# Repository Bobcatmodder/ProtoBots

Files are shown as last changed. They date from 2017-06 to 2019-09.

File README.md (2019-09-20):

# The ProtoBot project

https://theprotobotproject.wordpress.com

https://www.instructables.com/id/How-to-Build-the-ProtoBot-a-100-Open-Source-Super-/

Welcome! The goal of this project to create a robot platform that's

Simple and easy to use

    With a total of 2 motors, and 4 sensors, the ProtoBot is a very simple robot.
    Don’t let it fool you, though! You can still do a lot with it, especially with programming. 
    It’s also very easy to build. In our experience, a middleschooler can build one in several
    hours, including soldering the board.

Low Cost and Accessible

    Using cheap, common components, the ProtoBot is easily sourced online. The plastic parts 
    can be printed on any 3D printer that has a  build volume over 10x10x5, or ordered from a
    3D printing service online. The PCB can be either hand etched, or obtained through a 
    PCB prototyping service.

100% Open Source

    Everything is open source, even the guides. That means anyone can:

      Download all design files, source code, and documentation free of charge
      Modify all or any part of the work
      Distribute the original, or modified versions of the work
      Sell copies of the original, or modified work

NOTE: Still a work in progress- If anything's missing, please contact me!

Liscense notes:
    All the hardware design files, and Arduino software/programs are under MIT liscenses. 
    All the Guides and instructions are under CC Attriution 4.0 liscenses. 

    To credit me on a website or document, simply link to my GitHub here. PCBs and STL files need not include any form of direct credit, assuming any modified versions you upload to the internet have a link to my GitHub, credited as the original project. Code can simply have a line at the top that says something like "Based off of original code by Jacob Field, the ProtoBotProject" and a the GitHub URL. Basically, make sure people are able to find the original project from your modification, if they wish.

If you have any questions about this or anythign else, feel free to contact me. There's a contact form on the website that goes directly to my personal email.

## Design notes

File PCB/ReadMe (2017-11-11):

Etchable and Gerber files for the circuit boards. 

I've used PCBWay to make the boards, and so far I've been quite happy with both quality and prices.

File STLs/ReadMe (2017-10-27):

STL files. 
These can be printed at 0.2 MM resolution, and require no rafts or supports.

Usually I print the base at 103% scale, and the antenna parts at 105%, to ensure everything fits. It depends on how precise your printer is. I also usually scale the PCB supports to be twice as tall, cause they're not really tall enough as is.

The "4Antenna" file is just 4 antenna pieces in one STL, so that you can fit more on a printbed.

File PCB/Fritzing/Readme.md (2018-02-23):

Here are the fritzing files for the PCB, in case anyone wants to modify it.

Ideally you should credit my original design somewhere on the board, linking to the GitHub, or at least including the keywords "ProtoBot", if you release your own version.
Linking to the github isn't nessesary if you link to my original project here on your project page.

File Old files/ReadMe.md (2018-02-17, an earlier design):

A place to keep all the old files and such, in case anyone needs them.

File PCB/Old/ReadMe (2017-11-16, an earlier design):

These are older board designs. I'm just keeping them around in case newer versions don't work.

Should be functionally the same, but missing the Open Source Hardware logo and website URL,
as well as a few minor resistor placement changes and silkscreen images.

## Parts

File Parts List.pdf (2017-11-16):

## ProtoBot parts list:

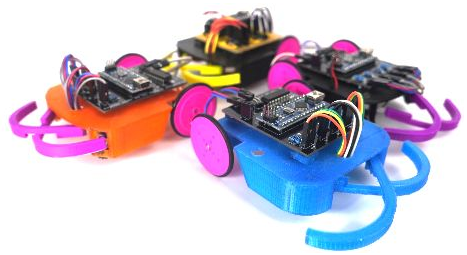
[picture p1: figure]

Quantities are enough for 1 complete robot

- 2 x N20 Gear motors (http://www.ebay.com/itm/6-12V-300-600-30RPM-Mini-DC-Metal-Gear-Motor-with-Gearwheel-Shaft-Diameter-N20-/172367169254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) (300RPM, 12V)
- 1 x Plastic Wheels (https://www.ebay.com/itm/10PCS-18-20-22-30-39mm-Synchronous-Belt-Triangle-Plastic-Pulley-Wheel-Toy-Parts/331665282711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) (39mm Yellow (3mm) - One lot is enough for 5 robots)
- 1 x Tactile Switches (http://www.ebay.com/itm/Pro-10PCS-Tact-Switch-KW11-3Z-5A-250V-Microswitch-3PIN-Buckle-Black-New-Arrivals-/391646361528) (Bump Sensors, One lot is enough for 5 robots)
- 1 x L293D Motor Driver IC (https://www.ebay.com/itm/2Pcs-L293D-L293-Push-Pull-Four-Channel-Motor-Driver-IC-NEW-C/141976513714) (One lot is enough for 2 robots)
- 1 x Wires (https://www.ebay.com/itm/40Pcs-1P-1P-2Pin-Header-2-54mm-Female-to-Female-Dupont-Line-Connector-Wire-Cable/282271776128) (Female to female jumper wires - One lot is enough for 4 robots)
- 1 x Headers (http://www.ebay.com/itm/5pcs-1-40-40Pin-2-54mm-20mm-Long-Header-Pin-Male-Breakable-Pin-Header-CA-/141976508934) (One lot is enough for 10 robots)
- 1 x 9V battery Clips (http://www.ebay.com/itm/10-pcs-9V-9-Volt-Battery-Clip-Connector-Soft-Shell-Black-w9-/172489325525) (One lot is enough for 10 robots)
- 1 x 10K resistors (http://www.ebay.com/itm/100pcs-1-4w-Watt-10K-ohm-10Kohm-Metal-Film-Resistor-0-25W-100000R-1-/141976458420) (One lot is enough for 25 robots)
- 1 x 220 Ohm resistors (https://www.ebay.com/itm/100-PCS-1-4W-0-25W-5-220-R-OHM-Carbon-Film-Resistor-1st-Class-Postage-UK-U5C7/332361071234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) (One lot is enough for 50 robots)
- 1 x Arduino Nano (https://www.ebay.com/itm/1-2-5-PCS-USB-Nano-V3-0-ATmega168-16M-5V-Mini-controller-CH340G-For-Arduino/253086177630) (ATEMGA328P module, not interface base module)
- 1 x Reflective IR optical sensor (http://www.ebay.com/itm/252618720538?_trksid=p2055119.m1438.l2649&ssPageName=STRK%3AMEBIDX%3AIT) (Enough for 5 robots, here’s (https://www.ebay.com/itm/100PCS-TCRT5000L-TCRT5000-Reflective-Optical-Sensor-Infrared-IR-Switch-infrared/253141705866) enough for 50)
- 1 x Female header pins (https://www.ebay.com/itm/10X-Single-Row-Straight-Female-Pin-Header-Connector-Strip-Arduino-2-54mm-CB/201874127141) (One lot is enough for a lot of robots)

Links updated 11/16/17

Copyright © 2017, Jacob Field. This work is licensed under a Creative Commons Attribution 4.0 International License. (http://creativecommons.org/licenses/by/4.0/)

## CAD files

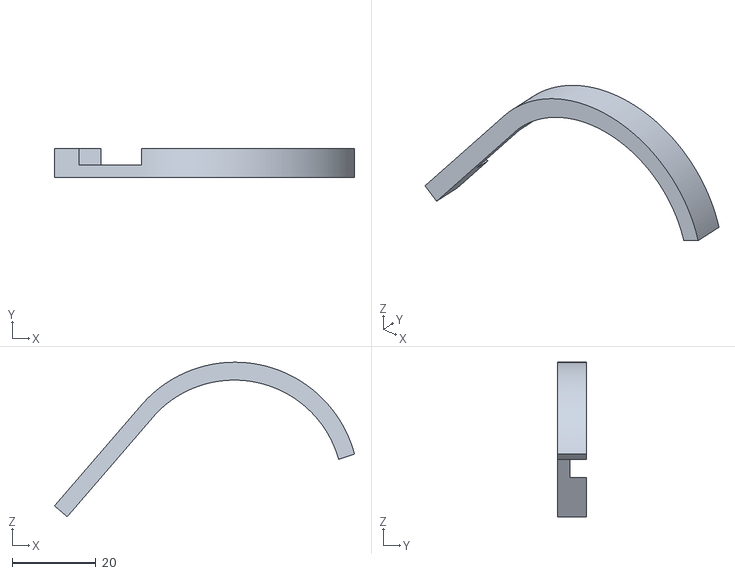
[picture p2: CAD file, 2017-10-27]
STLs/Antenna.stl
71.6 x 7.00 x 36.9

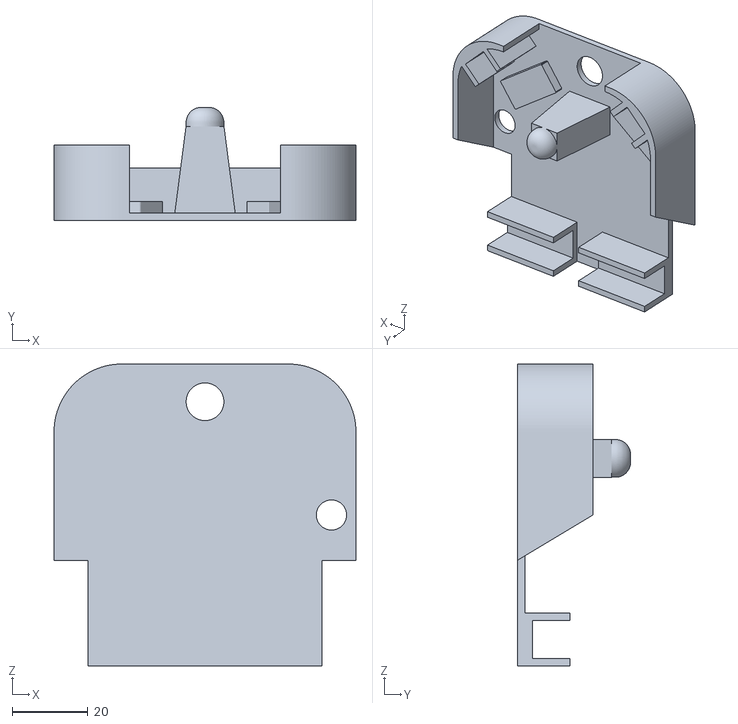
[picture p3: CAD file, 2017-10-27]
STLs/Base.stl
80.0 x 30.0 x 80.0

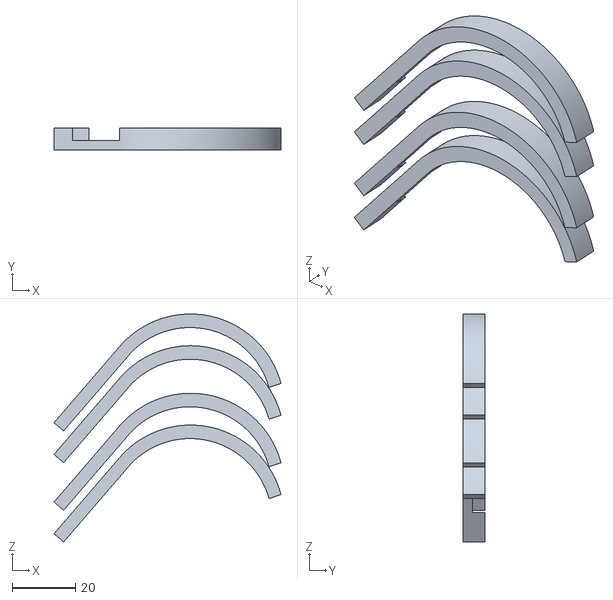
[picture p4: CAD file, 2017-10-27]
STLs/4Antenna.stl
71.6 x 7.00 x 71.9

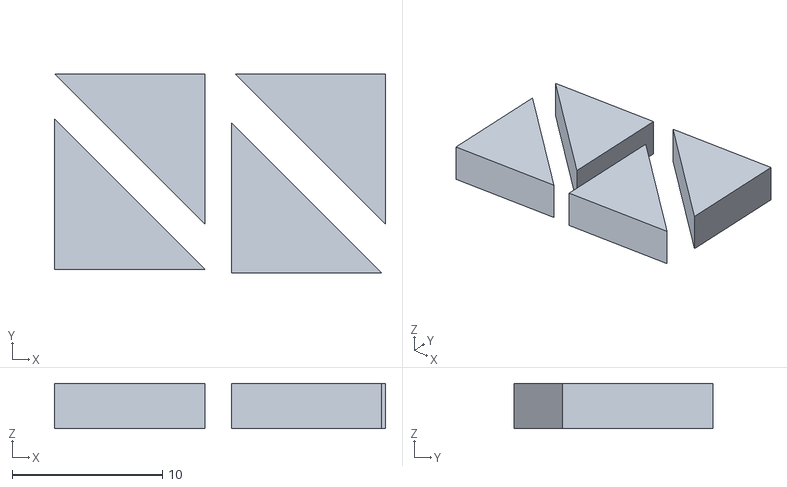
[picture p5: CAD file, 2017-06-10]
STLs/ProtoBotPCBSupport.stl
22.0 x 13.2 x 3.00

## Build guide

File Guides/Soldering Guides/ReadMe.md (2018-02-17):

These are guides for soldering the different major components in the ProtoBot.

For an online (Instructables) version, visit https://www.instructables.com/id/How-to-Build-the-ProtoBot-a-100-Open-Source-Super-/

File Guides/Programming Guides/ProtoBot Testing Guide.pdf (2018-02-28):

## Testing your Protobot

Now that your protobot is built, let’s test it to make sure everything works!

Plug the robot into your computer, using a USB cable.

On the desktop, look for the Arduino icon. If you can’t find it there, try searching for “Arduino” in the start menu.

Double click the icon to start the Arduino editor.

Once the Arduino IDE
is started, click on
“File”, then
“Examples”, and scroll
all the way down.

You should see
“ProtoBotV03”. Click
on that, and then
click on
“ProtoBotExplorer”.

This is the example
program we’ll use to
test your robot.

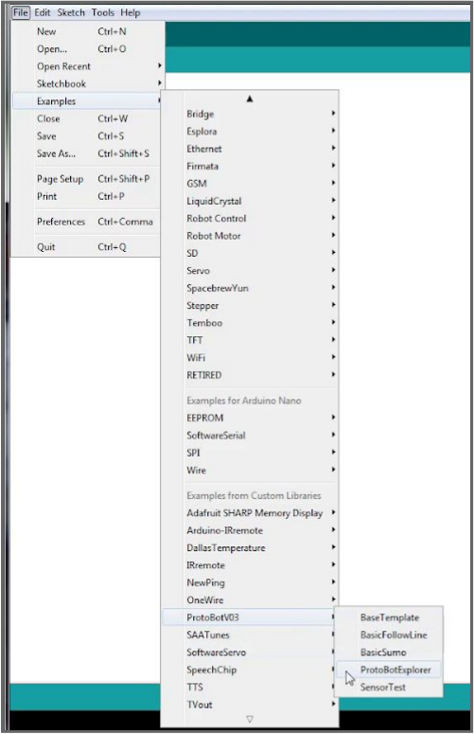
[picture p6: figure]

Copyright © 2017, Jacob Field. This work is licensed under a Creative Commons Attribution 4.0 International License. (http://creativecommons.org/licenses/by/4.0/)

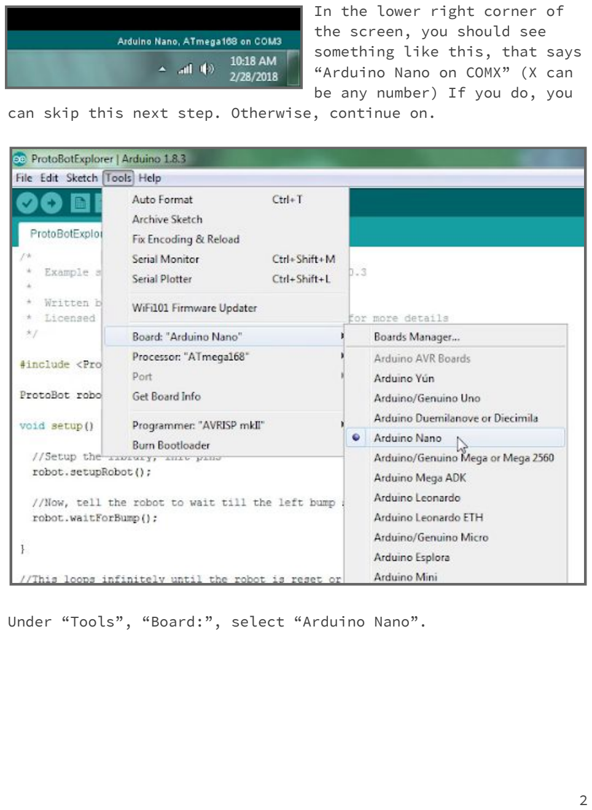
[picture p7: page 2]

In the lower right corner of the screen, you should see something like this, that says “Arduino Nano on COMX” (X can be any number) If you do, you can skip this next step. Otherwise, continue on.

Under “Tools”, “Board:”, select “Arduino Nano”.

2

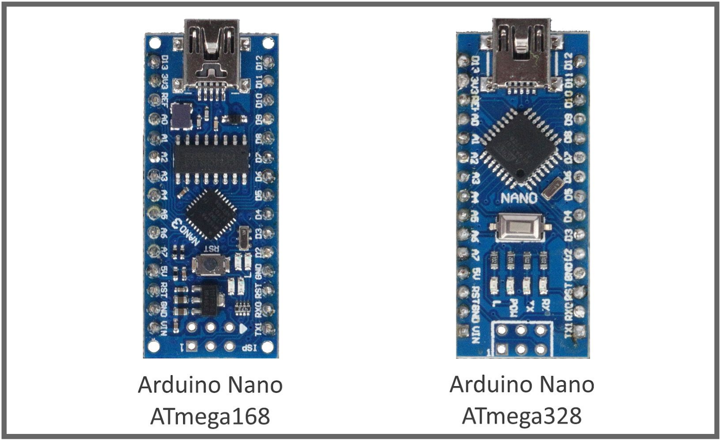
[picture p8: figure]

Look at the Arduino
board on your robot
to determine which
kind it is.

Then, under “Tools”,
“Processor”, select
which kind your
board is.

It can either be an
“ATmega168” or
“ATmega328”. If
you’re not sure, try
one, then the other.

Next, select which
port your arduino is
connected to, under
“Tools”, “Port”.
Usually there will
be one option,
select that.

If there are several
options, try each
one until one works.

3

Up in the top left corner of the Arduino editor, you’ll see several buttons.

The checkmark button tests your program to make sure there are no errors, and the right facing arrow (upload) button

sends the program to the robot.

Go ahead and click on the upload button! A progress bar down at the bottom of the screen will tell when it’s done.

Once your program has finished uploading to the robot, unplug the robot, put it on the floor, plug the battery in, and bump the bumpers to start it!

If everything works, great! You can skip the rest of this! If it isn’t quite working right, no fear! That’s perfectly normal, and should be easy to fix.

Is the robot:

- Spinning in circles, or driving backwards?
- The motors may be reversed. Figure out which ones are going backwards, and switch how the wires are plugged into the board.
- Constantly backing up and turning?
- One of the line sensors are probably plugged in wrong. Figure out which one is being triggered, and then make sure the wires are plugged in correctly!
- Doing something else that’s weird?
- The most common cause of robot troubles is sensors or motors plugged in wrong. Make sure everything is correctly plugged in, and if that doesn’t work, take it to a camp helper or mentor.
4

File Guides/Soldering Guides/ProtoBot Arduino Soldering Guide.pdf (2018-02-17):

# ProtoBot Arduino Soldering Guide

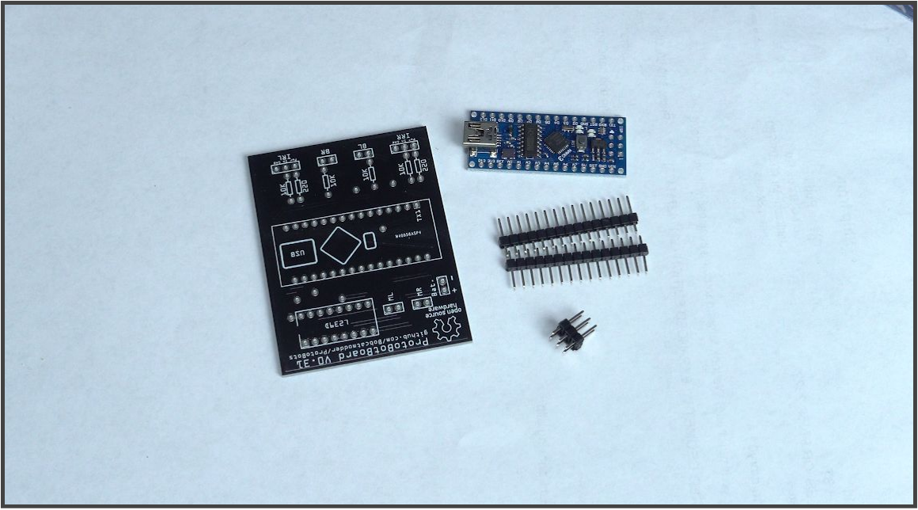
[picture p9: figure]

### You will need:

Parts:
- 1 x Arduino with pin headers (comes in a little antistatic baggy)

Tools:
- Soldering iron with fine tip

Note: The board is nice to have on hand to keep the pins at the correct angle while soldering.

Copyright © 2018, Jacob Field. This work is licensed under a Creative Commons Attribution 4.0 International License. (http://creativecommons.org/licenses/by/4.0/)

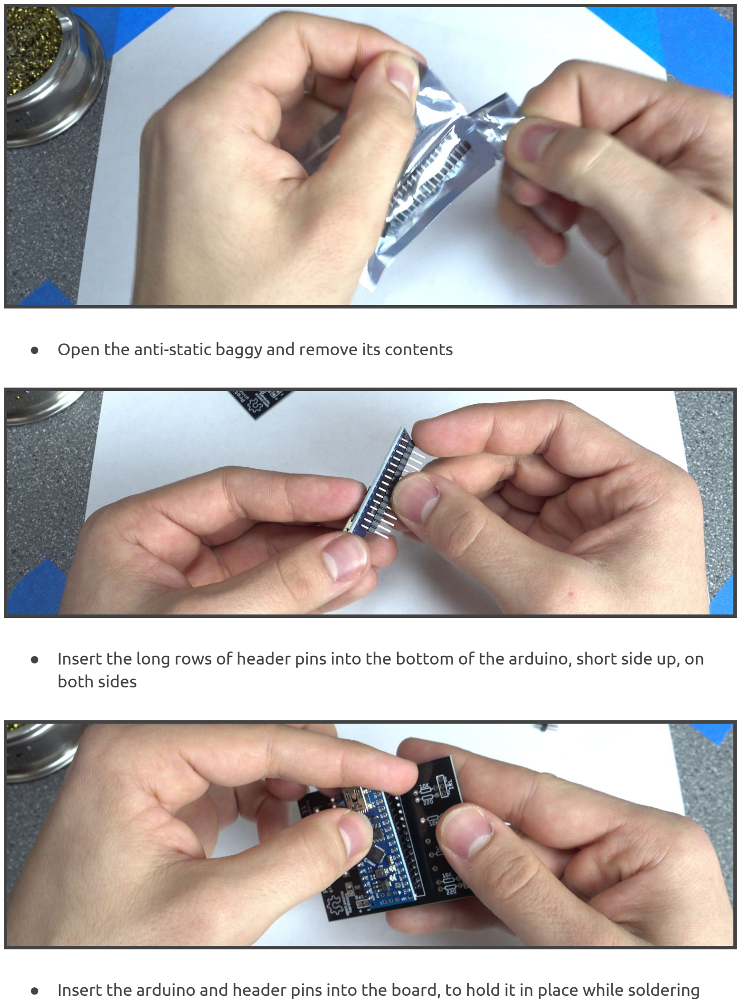
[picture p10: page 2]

- Open the anti-static baggy and remove its contents
- Insert the long rows of header pins into the bottom of the arduino, short side up, on both sides
- Insert the arduino and header pins into the board, to hold it in place while soldering

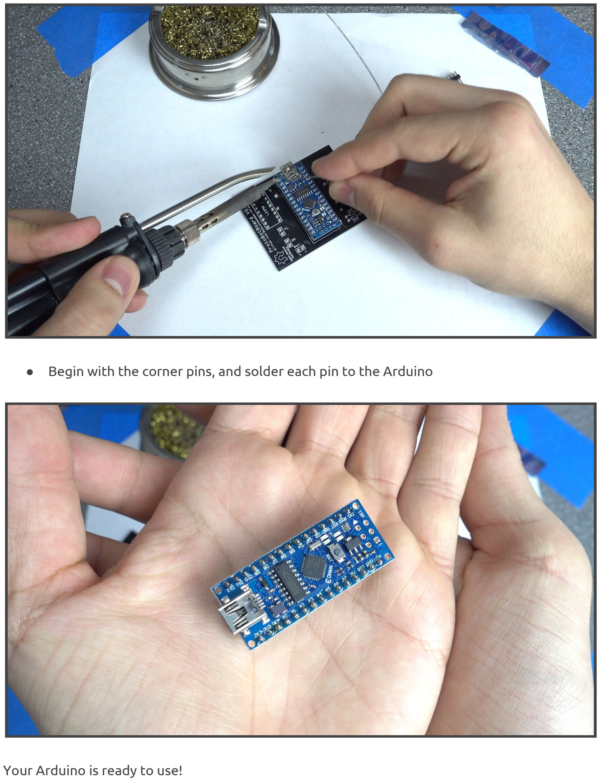
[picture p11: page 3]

- Begin with the corner pins, and solder each pin to the Arduino

Your Arduino is ready to use!

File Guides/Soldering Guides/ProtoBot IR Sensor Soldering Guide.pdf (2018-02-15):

# ProtoBot IR Sensor Soldering Guide

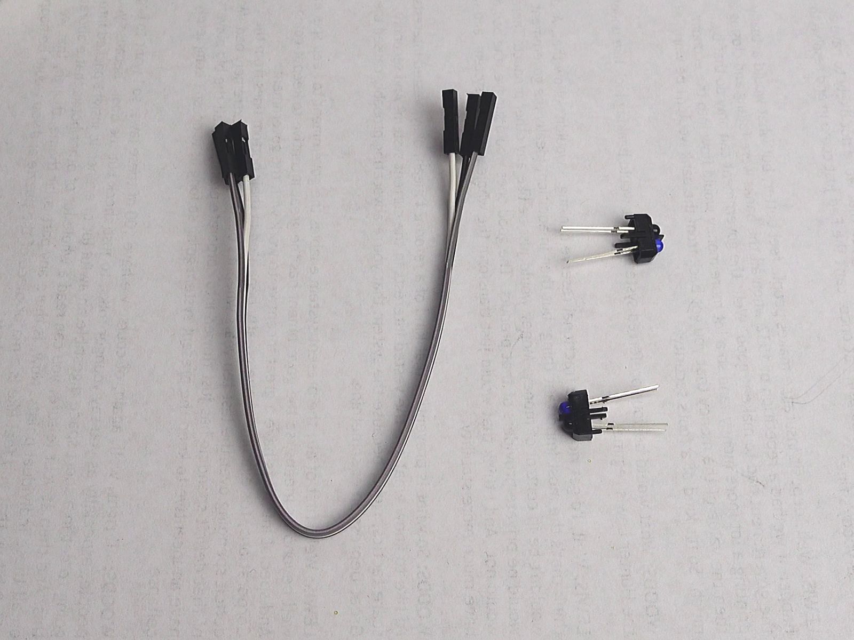
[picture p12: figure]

### You will need:

Parts:
- 2 x IR Sensors
- 1 set of two DuPont Female-Female jumper wires

Tools:
- Wire cutters/Strippers
- Soldering Iron with Fine tip
- Helping Hands, or something to hold the bump sensors in place (I used tape)

Copyright © 2018, Jacob Field. This work is licensed under a Creative Commons Attribution 4.0 International License. (http://creativecommons.org/licenses/by/4.0/)

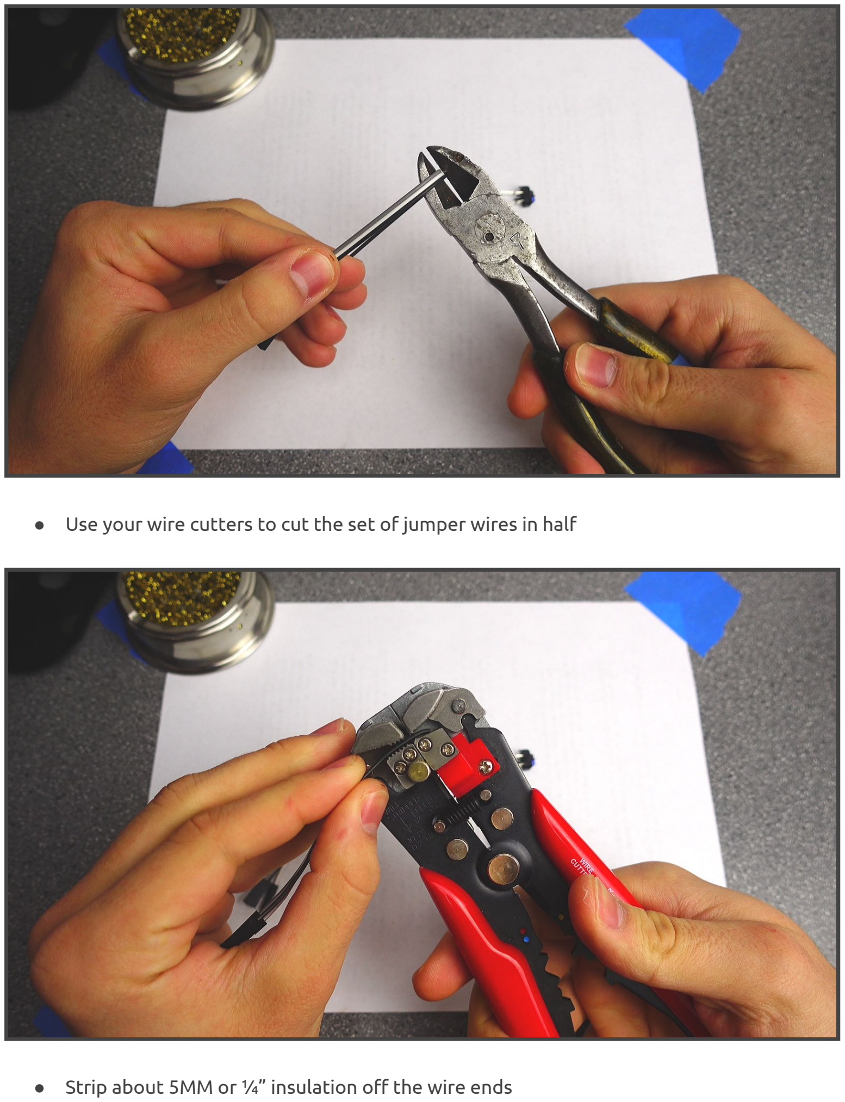
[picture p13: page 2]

- Use your wire cutters to cut the set of jumper wires in half
- Strip about 5MM or ¼” insulation off the wire ends

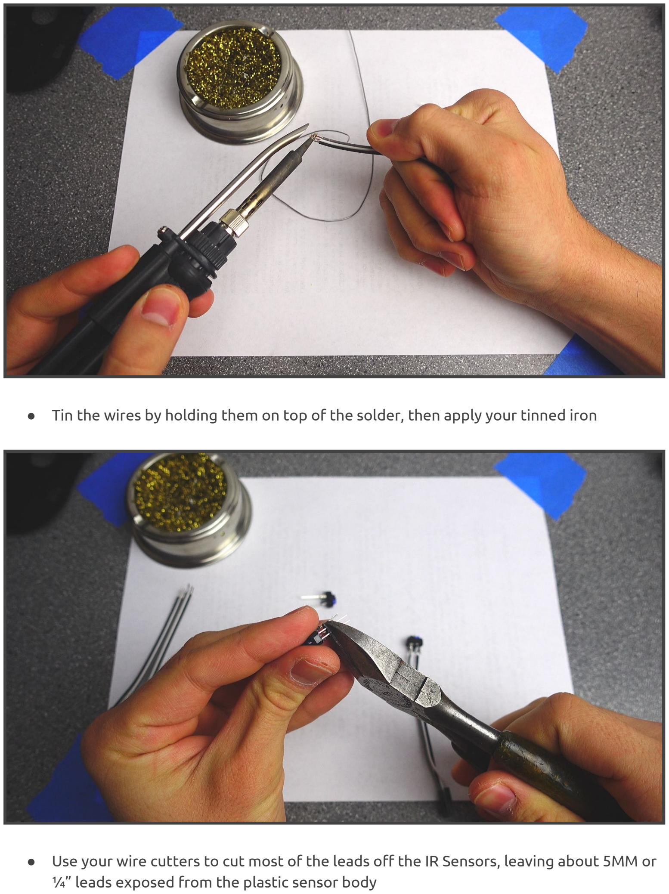
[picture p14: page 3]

- Tin the wires by holding them on top of the solder, then apply your tinned iron
- Use your wire cutters to cut most of the leads off the IR Sensors, leaving about 5MM or ¼” leads exposed from the plastic sensor body

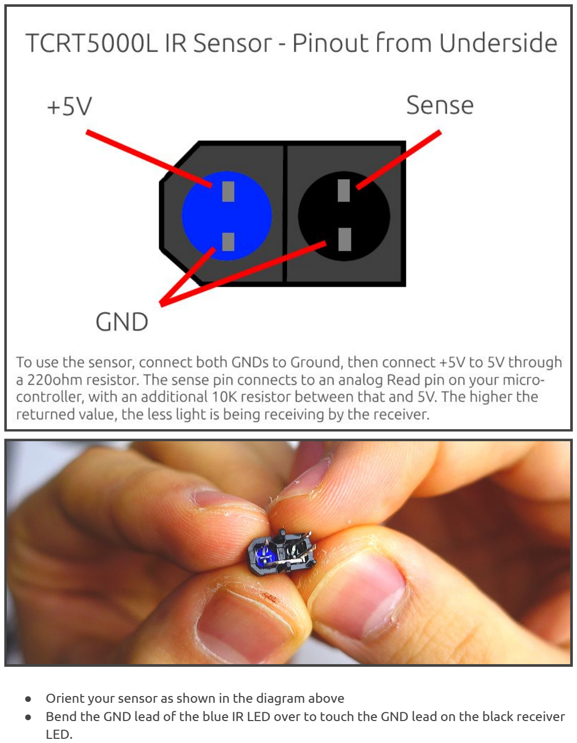
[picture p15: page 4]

- Orient your sensor as shown in the diagram above
- Bend the GND lead of the blue IR LED over to touch the GND lead on the black receiver LED.

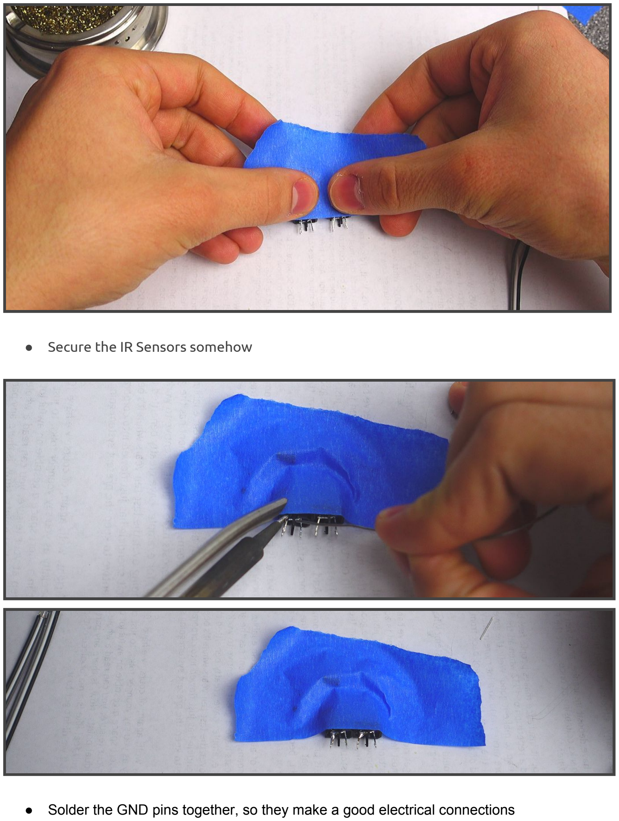
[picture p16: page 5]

- Secure the IR Sensors somehow
- Solder the GND pins together, so they make a good electrical connections

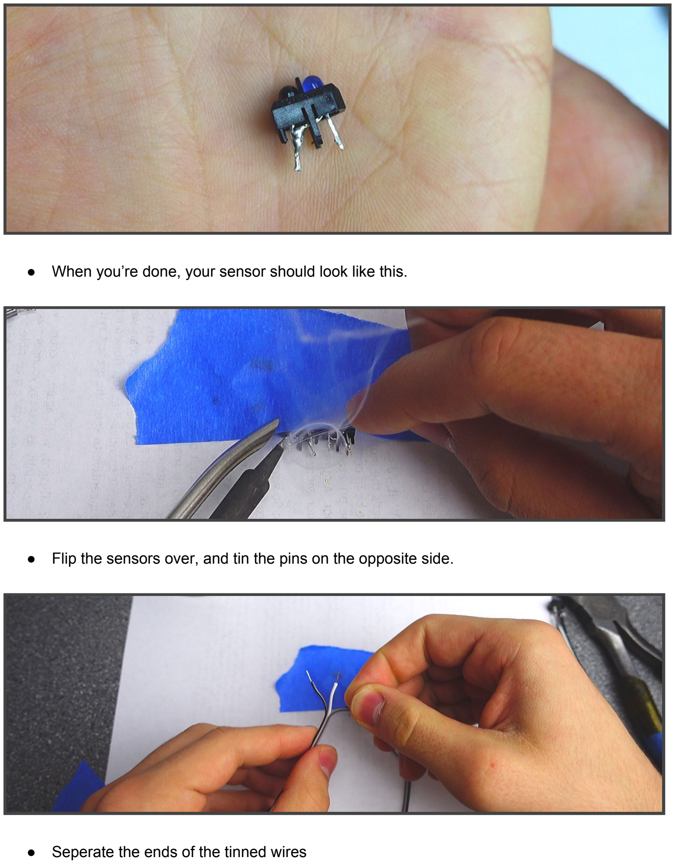
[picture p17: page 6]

- When you’re done, your sensor should look like this.
- Flip the sensors over, and tin the pins on the opposite side.
- Seperate the ends of the tinned wires

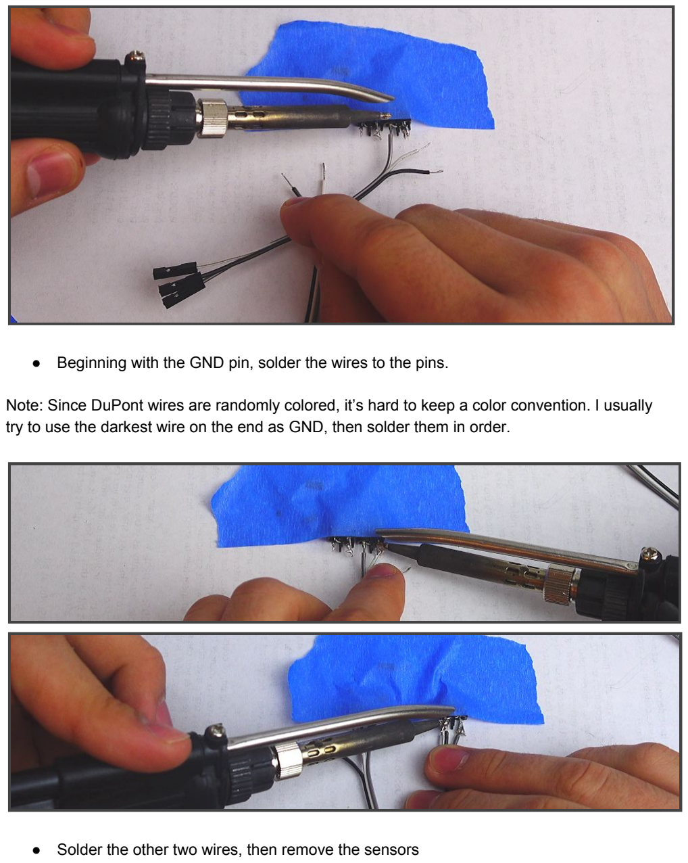
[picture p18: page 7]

- Beginning with the GND pin, solder the wires to the pins.

Note: Since DuPont wires are randomly colored, it’s hard to keep a color convention. I usually try to use the darkest wire on the end as GND, then solder them in order.

- Solder the other two wires, then remove the sensors

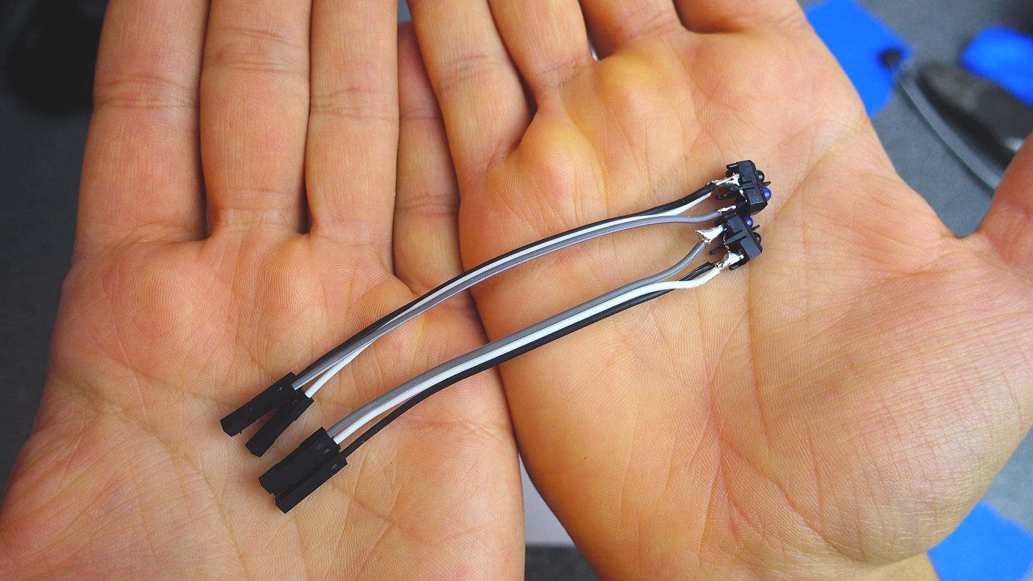
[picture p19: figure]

Your IR Sensors are ready to use on your ProtoBot!

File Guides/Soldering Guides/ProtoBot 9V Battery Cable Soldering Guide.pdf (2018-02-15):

# ProtoBot Battery Cable Soldering Guide

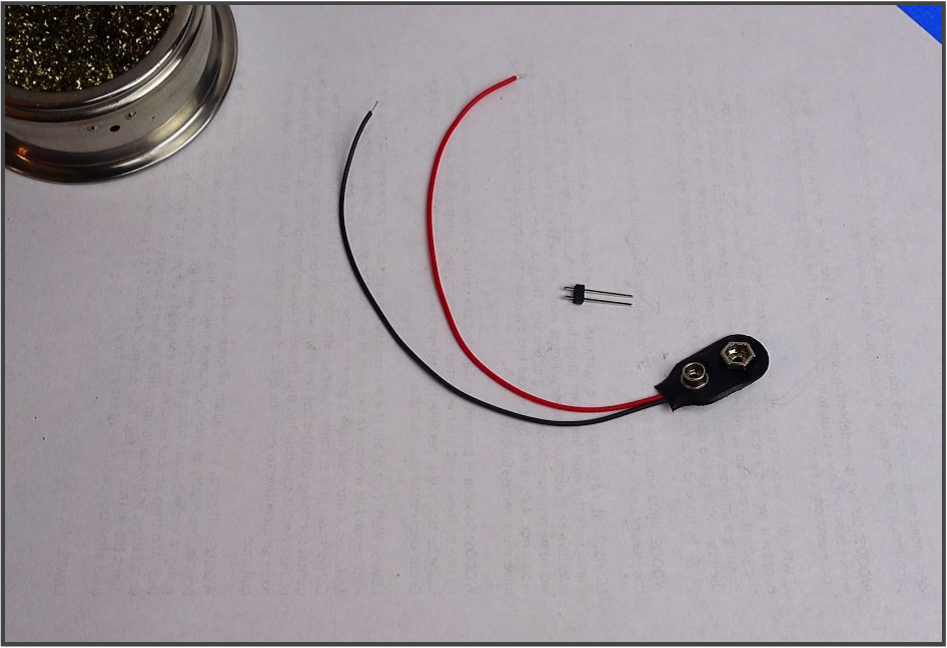
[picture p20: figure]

### You will need:

Parts:
- 1 x 9V battery cable
- 1 x 2-pin length of male pin headers

Tools:
- Soldering Iron with Fine tip
- Helping Hands, or something to hold the cable in place (I used foam and tape)

Copyright © 2018, Jacob Field. This work is licensed under a Creative Commons Attribution 4.0 International License. (http://creativecommons.org/licenses/by/4.0/)

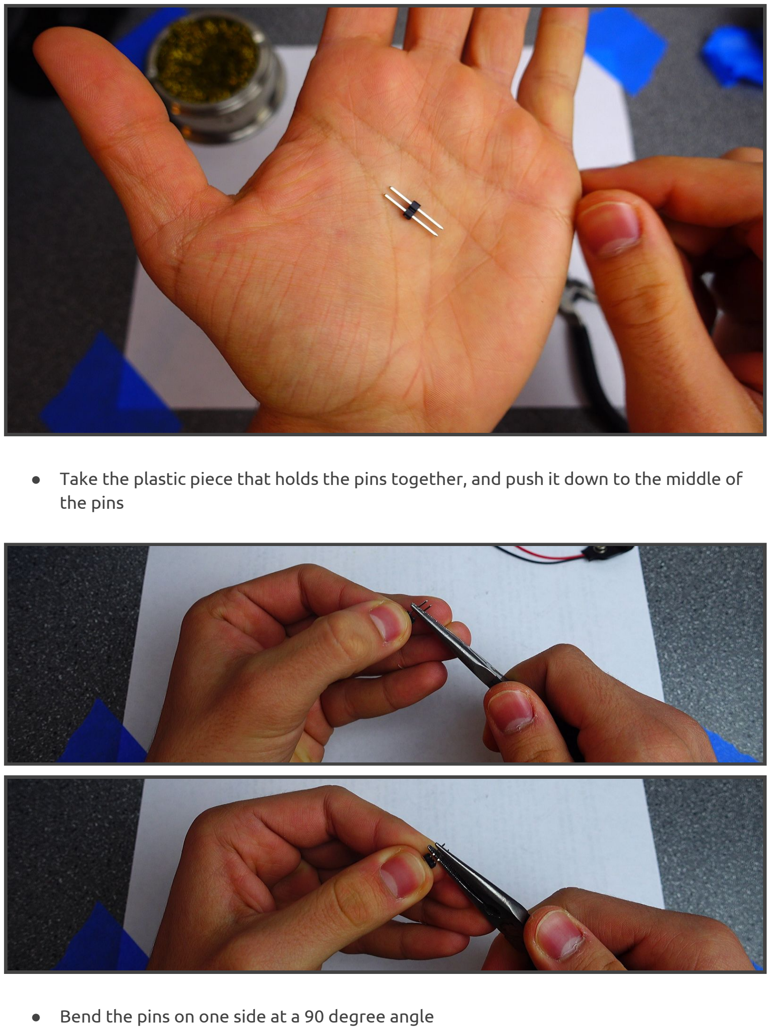
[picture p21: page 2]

- Take the plastic piece that holds the pins together, and push it down to the middle of the pins
- Bend the pins on one side at a 90 degree angle

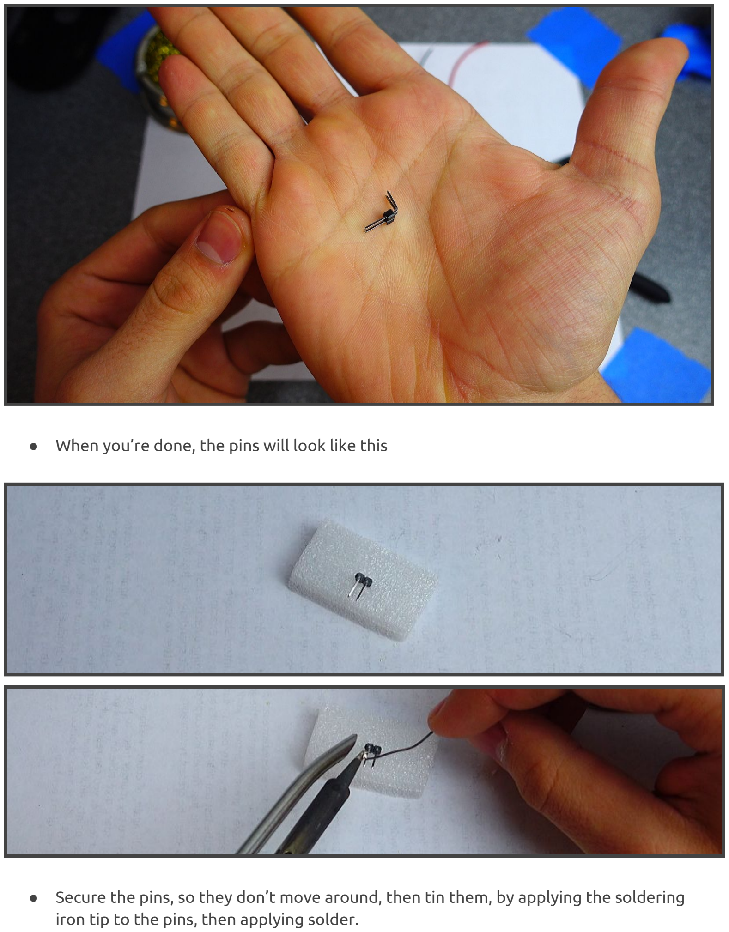
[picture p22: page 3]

- When you’re done, the pins will look like this
- Secure the pins, so they don’t move around, then tin them, by applying the soldering iron tip to the pins, then applying solder.

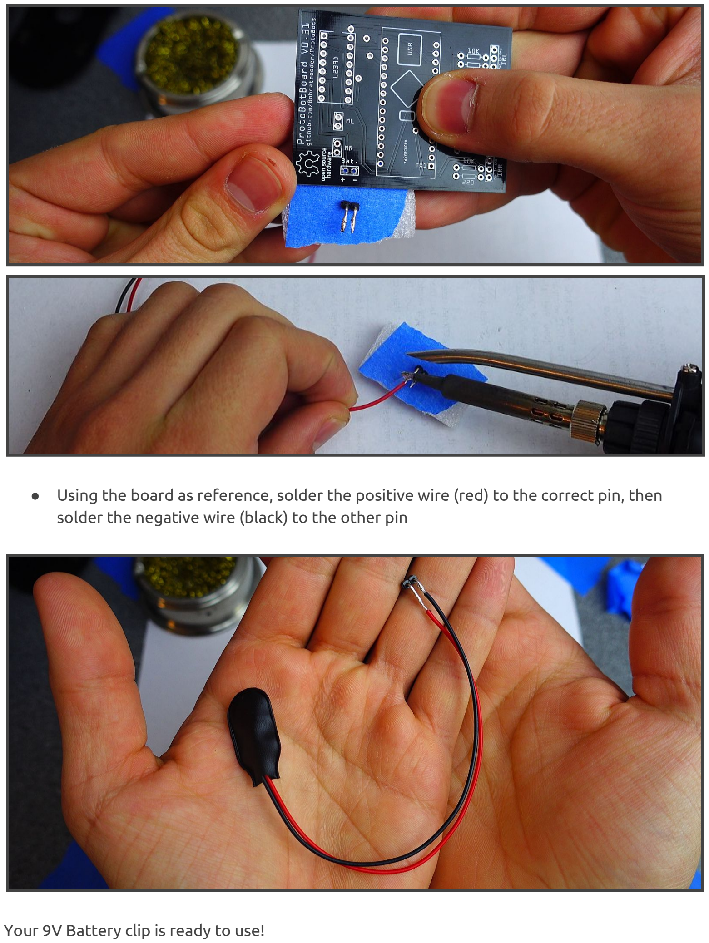
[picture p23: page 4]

- Using the board as reference, solder the positive wire (red) to the correct pin, then solder the negative wire (black) to the other pin

Your 9V Battery clip is ready to use!

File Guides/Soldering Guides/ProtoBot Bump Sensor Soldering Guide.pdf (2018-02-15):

# ProtoBot Bump Sensor Soldering Guide

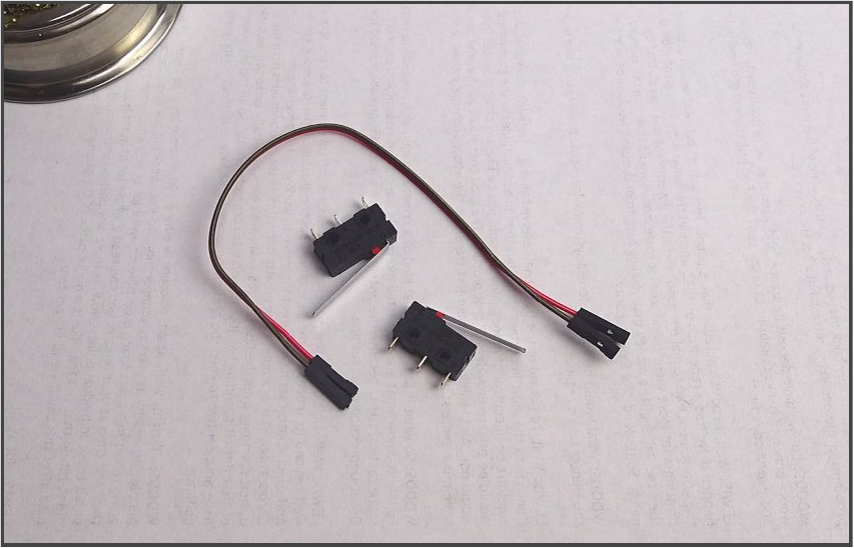
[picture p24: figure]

### You will need:

Parts:
- 2 x Limit Switches
- 1 set of two DuPont Female-Female jumper wires

Tools:
- Wire cutters/Strippers
- Soldering Iron with Fine tip
- Helping Hands, or something to hold the bump sensors in place (I used tape)

Copyright © 2018, Jacob Field. This work is licensed under a Creative Commons Attribution 4.0 International License. (http://creativecommons.org/licenses/by/4.0/)

- Cut your pair of wires in half
- Use your wire strippers to strip about 5MM or ¼” insulation off the ends

- Split the ends apart, then twist the loose strands on each wire end together
- Tin the wire ends, by holding them over the solder, then applying your tinned iron tip

- Secure the sensors so they won’t move around
- Bend the tinned ends of each wire so the wires are 180 degrees apart from each other

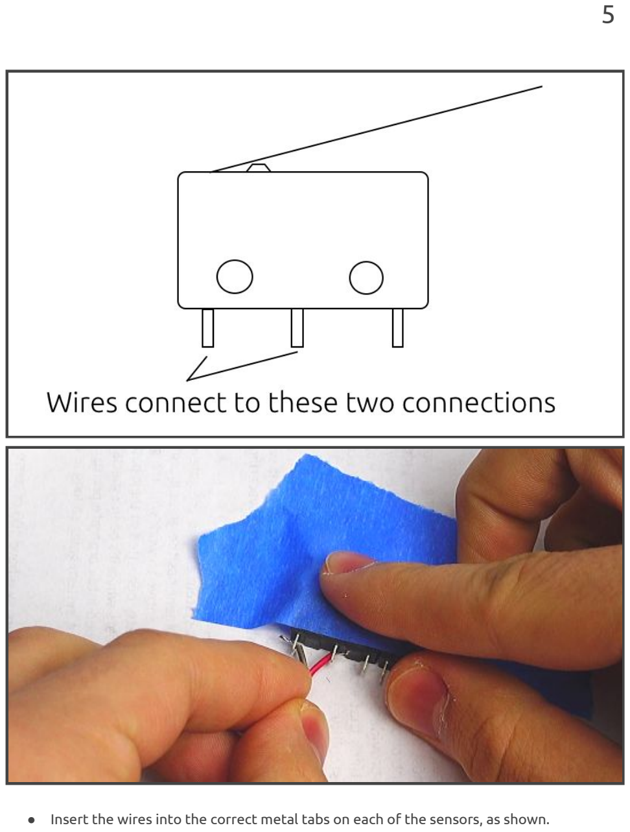
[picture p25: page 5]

- Insert the wires into the correct metal tabs on each of the sensors, as shown.

- Solder each of the wires to the metal tabs

Your bump sensors are now ready to be used on a ProtoBot!

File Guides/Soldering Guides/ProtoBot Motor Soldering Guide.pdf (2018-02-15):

# ProtoBot Motor Soldering Guide

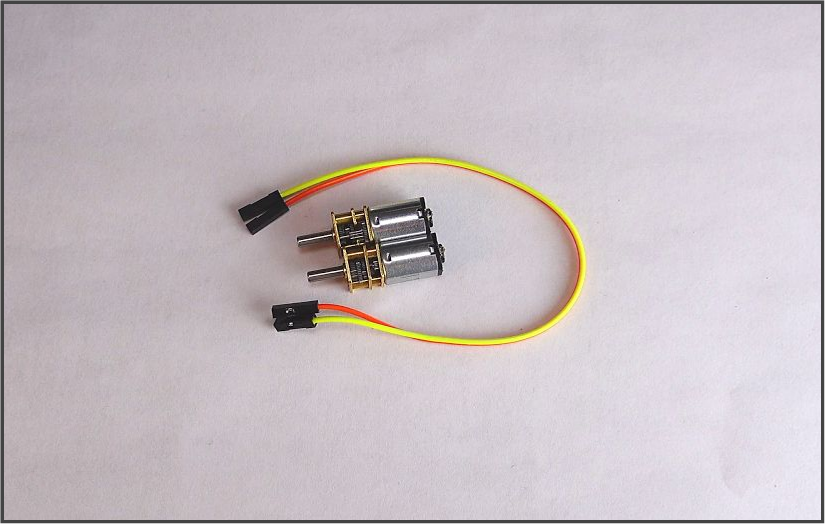
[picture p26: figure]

### You will need:

Parts:
- 2 x N20 Gear motors
- 1 set of two DuPont Female-Female jumper wires

Tools:
- Wire cutters/Strippers
- Soldering Iron with Fine tip
- Helping Hands, or something to hold the motors in place. (I used foam and tape)
- Hot Glue gun with Glue (High-Temp preferable)

Copyright © 2018, Jacob Field. This work is licensed under a Creative Commons Attribution 4.0 International License. (http://creativecommons.org/licenses/by/4.0/)

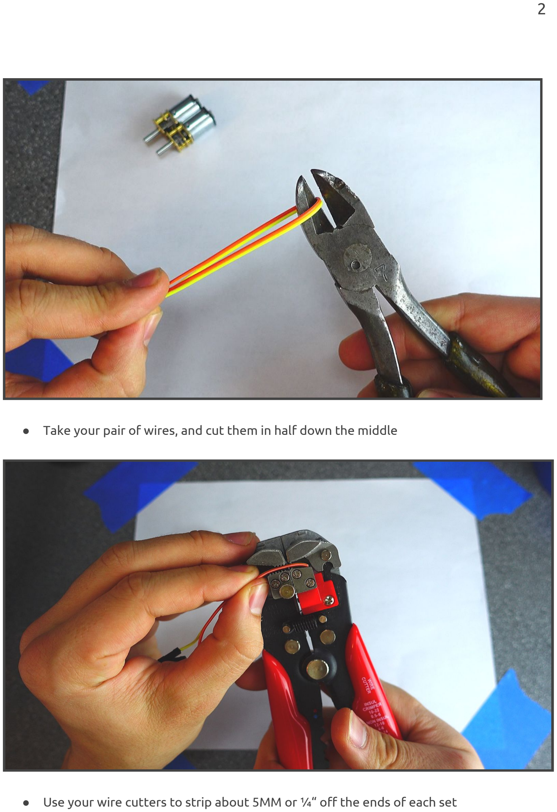
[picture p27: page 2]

- Take your pair of wires, and cut them in half down the middle
- Use your wire cutters to strip about 5MM or ¼“ off the ends of each set

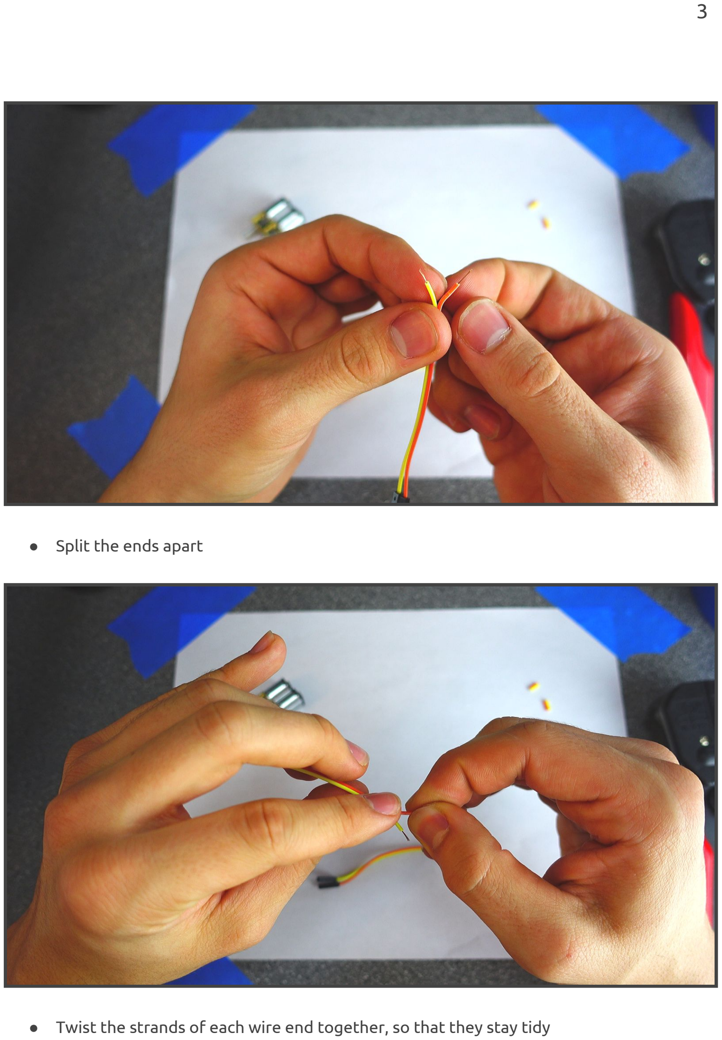
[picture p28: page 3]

- Split the ends apart
- Twist the strands of each wire end together, so that they stay tidy

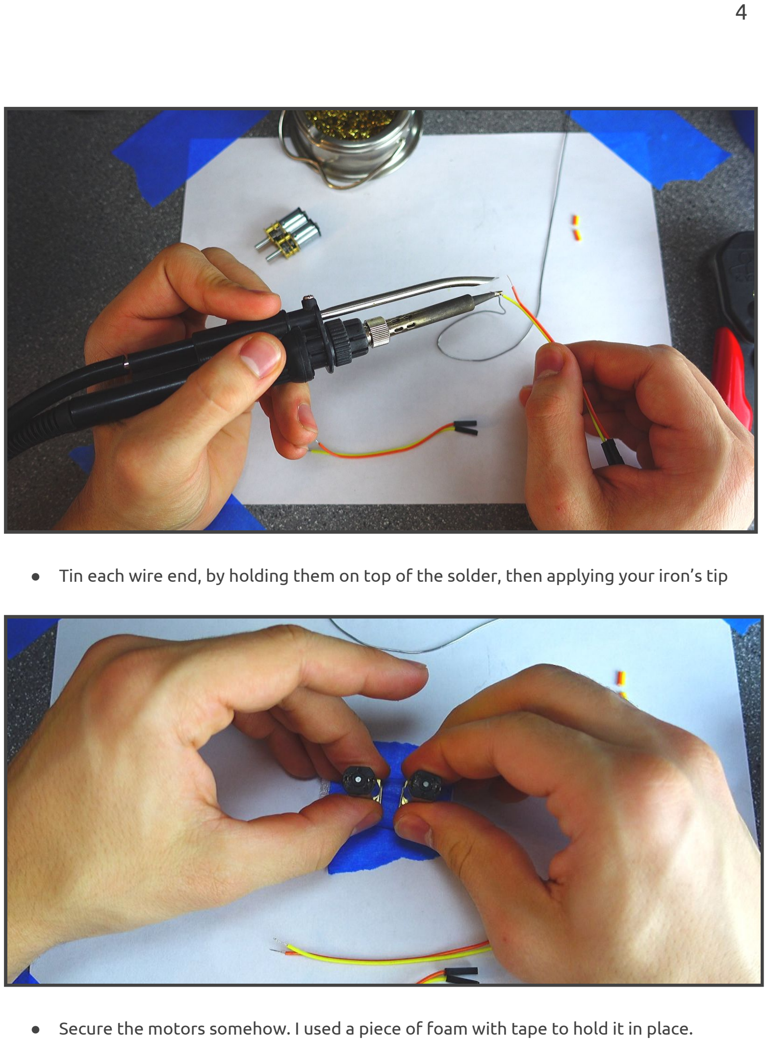
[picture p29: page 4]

- Tin each wire end, by holding them on top of the solder, then applying your iron’s tip
- Secure the motors somehow. I used a piece of foam with tape to hold it in place.

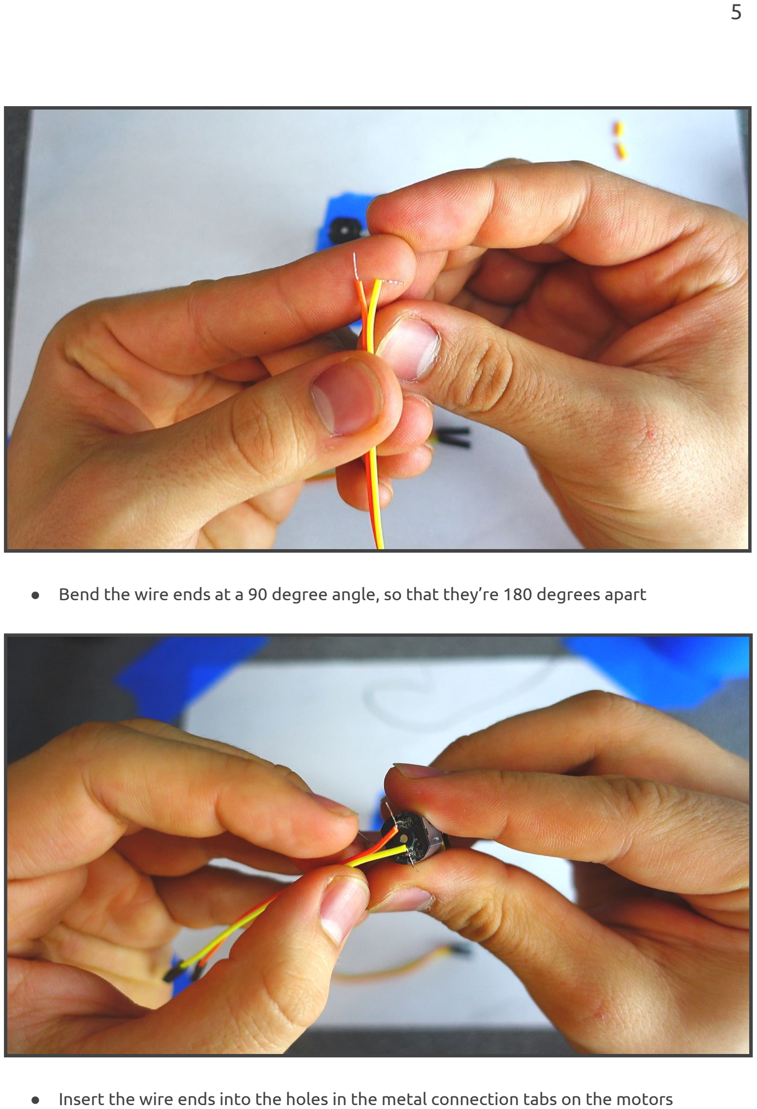
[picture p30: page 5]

- Bend the wire ends at a 90 degree angle, so that they’re 180 degrees apart
- Insert the wire ends into the holes in the metal connection tabs on the motors

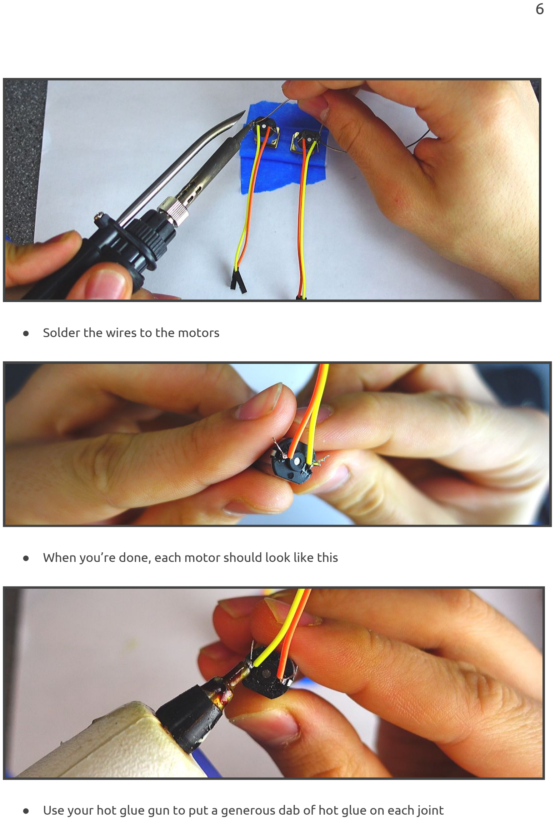
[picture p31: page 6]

- Solder the wires to the motors
- When you’re done, each motor should look like this
- Use your hot glue gun to put a generous dab of hot glue on each joint

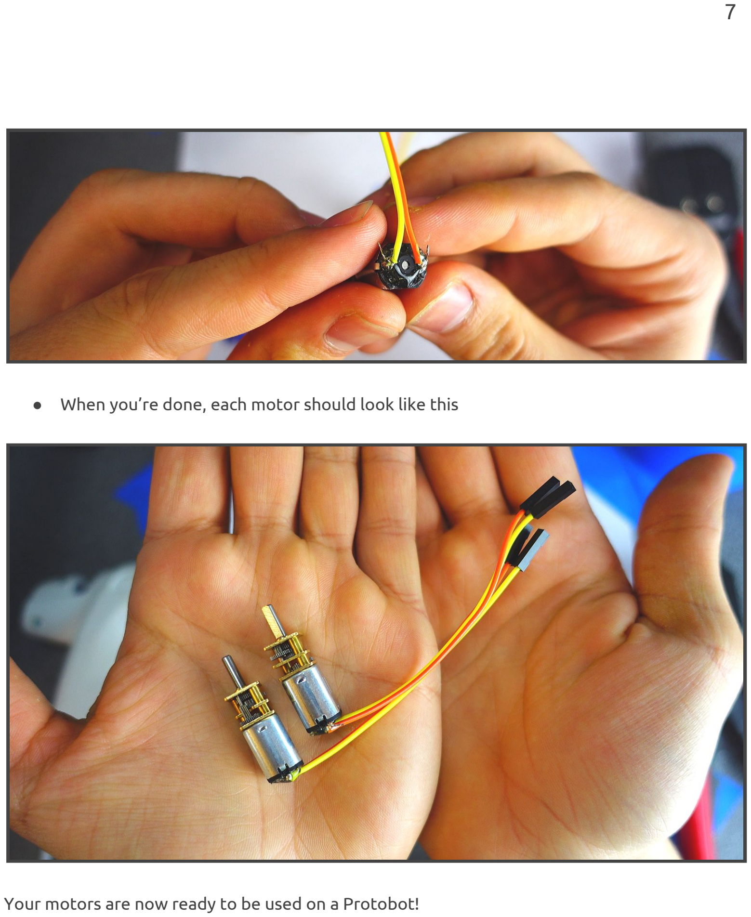
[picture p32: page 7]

- When you’re done, each motor should look like this

Your motors are now ready to be used on a Protobot!

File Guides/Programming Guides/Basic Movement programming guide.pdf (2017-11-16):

Basic | Movement | example

Now that you’ve tested your robot, and know it works, let’s try making it move ourselves.

Click on “File”, then “Examples”, then scroll all the way down the list, until you see “ProtoBotV03”. Click on that, then click on “BasicTemplate”. This is a clean template file, with no user code in it yet.

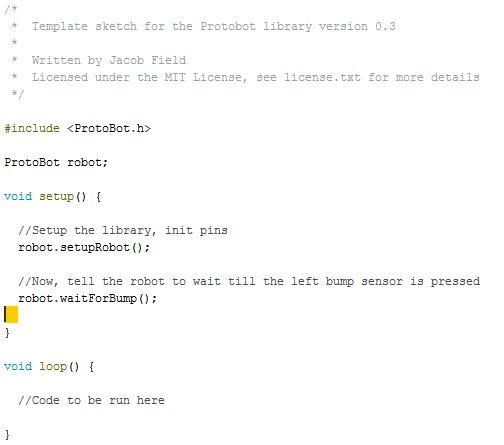
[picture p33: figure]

This is where we’ll be writing our code, where the highlight is, after the line of code that says “robot.waitForBump()”.

Copyright © 2017, Jacob Field. This work is licensed under a Creative Commons Attribution 4.0 International License. (http://creativecommons.org/licenses/by/4.0/)

## Moving the robot Forwards/Backwards:

Type the highlighted code into the arduino editor.

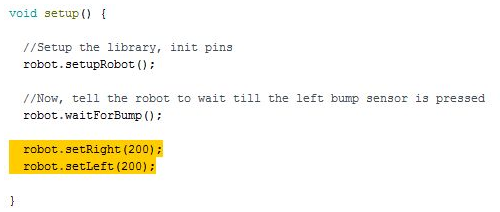
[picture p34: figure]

Here’s | how | it | works:
The “robot.setLeft” and “setRight” functions turn the motors on. The number inside the round “()” brackets are how fast the motors go.

Here, the number is 200, which is almost full speed ahead. The max speed is 255, -255 is full speed backwards, and 0 is stopped.

Try | uploading | the | program, | and | see | what | happens!
You might notice the motors never stop. That’s because we never told them to stop! How do you think we might stop them?

2

Here’s | the | code | to | stop | the | robot.
Go ahead and add it!

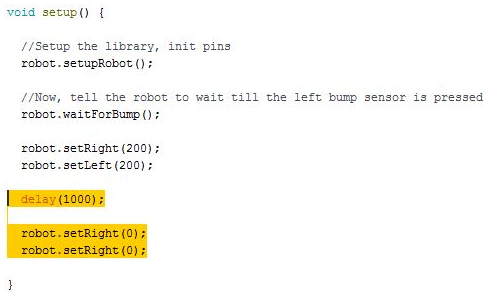
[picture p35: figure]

Here’s | how | it | works:
The “robot.setLeft(0)” and “robot.setRight(0)” lines tell the motors to turn off. But what does the “delay(1000)” do?

The “delay” function tells the robot to wait a certain amount of time. The number inside the round “()” brackets is how long to wait, in milliseconds. 1000 milliseconds is 1 second, 500 is half a second, and so on.

Try | changing | the | number | inside | the | round | brackets,
to see if you can get it to drive a certain distance!
Try | getting | the | robot | to | go | backwards!
You can change the speeds to -200 to make it go backwards.

3

## Turning the robot:

To turn, all you need to do is reverse one of the motors. That way, the robot will spin in a circle.

To reverse a motor, just add a “-” before the number inside the round brackets.

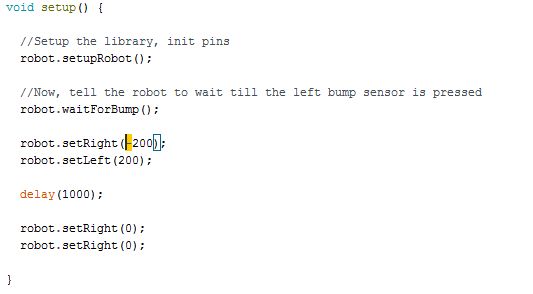
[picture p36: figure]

How | does | it | work?
By changing the value inside the “delay” function, you can control how long it turns.

By switching which motor is reversed, you switch which way it turns.

Try | turning | by | switching | one | motor | off, | instead!
Look at how this changes how your robot turns. Would this be a better way to turn?

4

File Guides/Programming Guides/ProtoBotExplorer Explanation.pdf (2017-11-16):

Example | program | Explanation

Now that you’ve uploaded the example program, let’s take a look at the code that makes the robot work.

Start at the top of the program.

The stuff in light grey is a comment. They’re just for us humans looking at the code, the robot ignores them. Comments either start with “/*”, or with “//”.

The next two lines just tell the programming program to include and set up the ProtoBot library. You probably won’t ever need to change these.

This is called a program control structure. Control structures help separate the code into different parts.

The “void startup” structure tells the robot what to do when it first starts running. Any code in it is run only once when the robot is given power, or reset.

Copyright © 2017, Jacob Field. This work is licensed under a Creative Commons Attribution 4.0 International License. (http://creativecommons.org/licenses/by/4.0/)

These two lines tell the program to set up some stuff for the library, and then tells the program to wait until the left bumper is pressed. You probably won’t need to change anything here, either.

Now we’re going to look at the “void loop” control structure. This “loop” runs over and over until the robot loses power, or is reset.

This is also where we’re going to write most of our code for the robot.

At the end of any control structure, you’ll see a curly bracket “}”. This tells the robot to stop looking for code inside of a control structure, so it’s important that they’re in the right place!

2

This is another control structure, called an “if” statement. It checks to see if the code inside the round brackets “()” is true, and if it is, runs the code inside the curly “{}” brackets.

Remember the curly brackets? Here, the open bracket “{“ tells the robot when to start looking for code, and the close “}” bracket tells it when to stop.

Any code you want to run if the “if” statement is true must be inside these brackets.

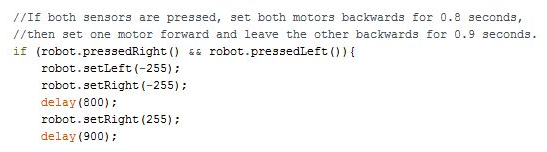
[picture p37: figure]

The example program uses a lot of “if” statements, to see if the robot has bumped into something, or run over an edge. It might look confusing, but it’s actually pretty easy to understand.

3

To begin, the “if” statement checks to see if either the Right or Left antenna are pressed. The “robot.pressedRight()” and “robot.pressedLeft()” statements check to see if either antenna is pressed, and the “&&” tells the “if” statement to run the code if either of those are true.

These two lines of code turn each motor on, at full speed backwards. The value inside the round brackets is what speed to use. 255 is full speed ahead, 0 is stopped, and -255 is full speed backwards. So, these lines of code make the robot go backwards at full speed.

This bit of code just tells the robot to wait for a certain amount of time, before it does the next thing. It will keep doing whatever you told it to do before until the time is up.

The number inside the round brackets is how long to wait, in Milliseconds. A millisecond is one thousandth of a second, so 1000 milliseconds is 1 second.

The rest of the code inside the “if” statement is pretty easy to understand. It sets the right motor at full speed ahead, so that the robot will spin, and waits for 900 milliseconds.

4

The curly bracket tells the robot that that’s the end of the code inside the “if” statement.

Take a look at the rest of the program. It should be pretty easy to understand, now that you know about “if” statements. You might notice that there’s a special kind of “if” statement being used, though. This is an “else if” statement.

An “else if” statement can only run if there is an “if” (or an “else if”) statement before it, and if that “if” or “if else” statement didn’t run, because the code inside the round brackets wasn’t true.

These are useful if you want the robot to only be able to do something if it wasn’t able to do something else.

Inside the “else if” statements, you’ll also notice another thing the robot can check for. The “robot.leftInfared()” and “robot.rightInfared()” functions check to see if either the left or right infrared (line) sensors are sensing a certain value inside the round brackets.

In this case, 800 is about right for sensing an edge.

5

At last, at the very end of the code, you’ll see another special statement. This is the “else” statement. An “else” statement is like an “else if” statement, but it will always run, if the “if” or “else if” statements before it didn’t run.

This is good if you want the robot to do something by default if it can’t do anything else.

6

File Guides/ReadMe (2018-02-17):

All the guides, in one handy place!

For an online version of the complete building guide, visit https://www.instructables.com/id/How-to-Build-the-ProtoBot-a-100-Open-Source-Super-/

More guides coming in multiple forms, as I make them.

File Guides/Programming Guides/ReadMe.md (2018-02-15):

All the programming guides:

Explinations of the main example program, and guides created to help kids learn how to program the robots.

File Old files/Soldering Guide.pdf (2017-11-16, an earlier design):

# Soldering Guide

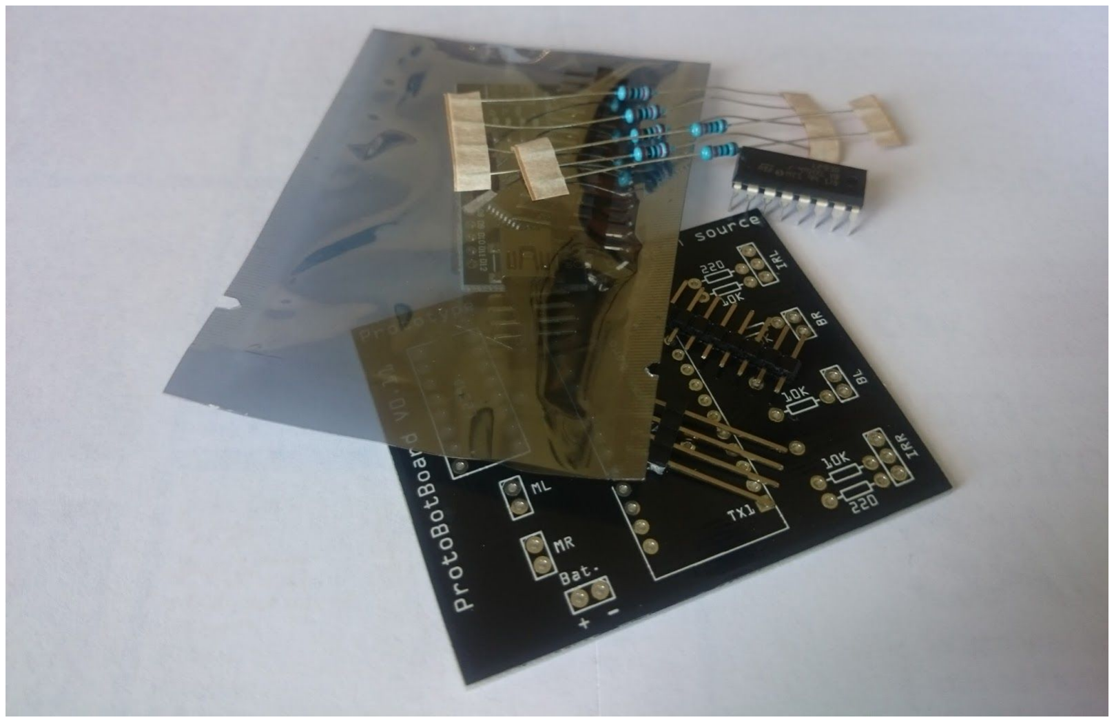
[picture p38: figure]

### You will need:

- ProtoBot circuit board
- Arduino Nano + Header pins (Should all be in a little baggy, unless your arduino is already assembled, or is soldered to the board)
- Motor Driver chip
- 2 x 220 Ohm resistors
- 4 x 10K Ohm resistors
- 4 x Long header pins
- 10 x short header pins
- 1 x Female header pins (Not pictured)
- Wire Cutters
- Masking tape
- Needle nose pliers

Copyright © 2017, Jacob Field. This work is licensed under a Creative Commons Attribution 4.0 International License. (http://creativecommons.org/licenses/by/4.0/)

# Step 1

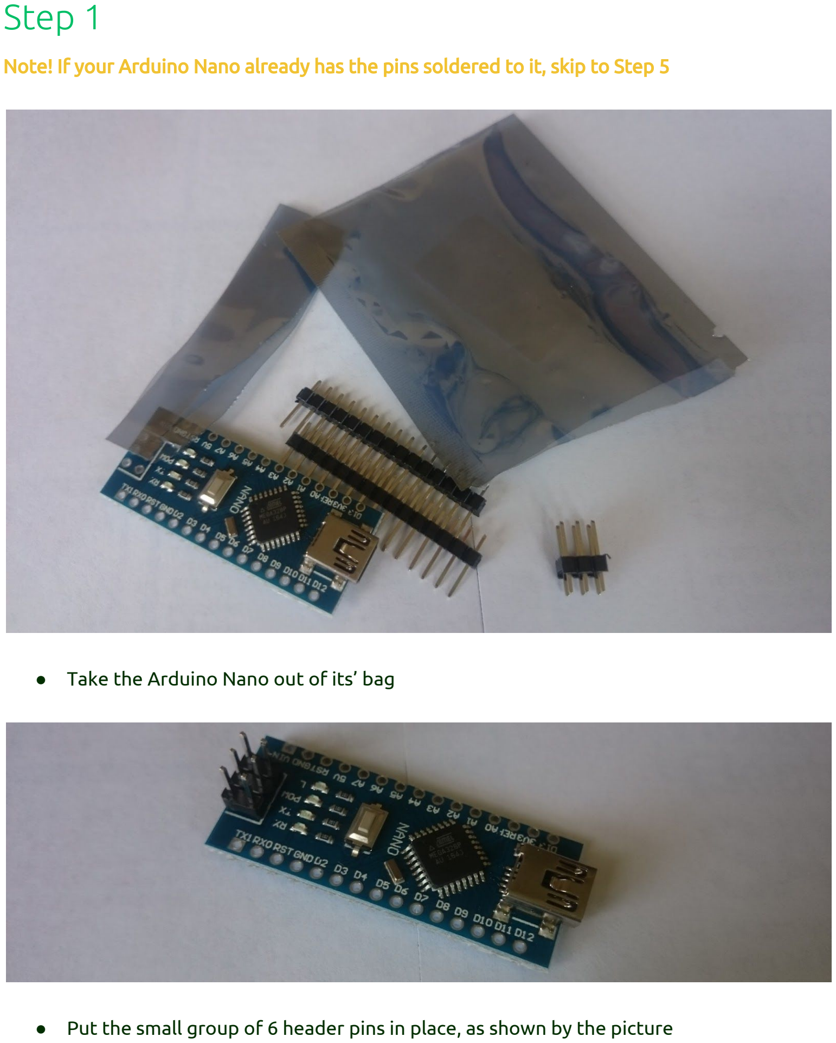
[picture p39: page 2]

Note! | If | your | Arduino | Nano | already | has | the | pins | soldered | to | it, | skip | to | Step | 5
- Take the Arduino Nano out of its’ bag
- Put the small group of 6 header pins in place, as shown by the picture

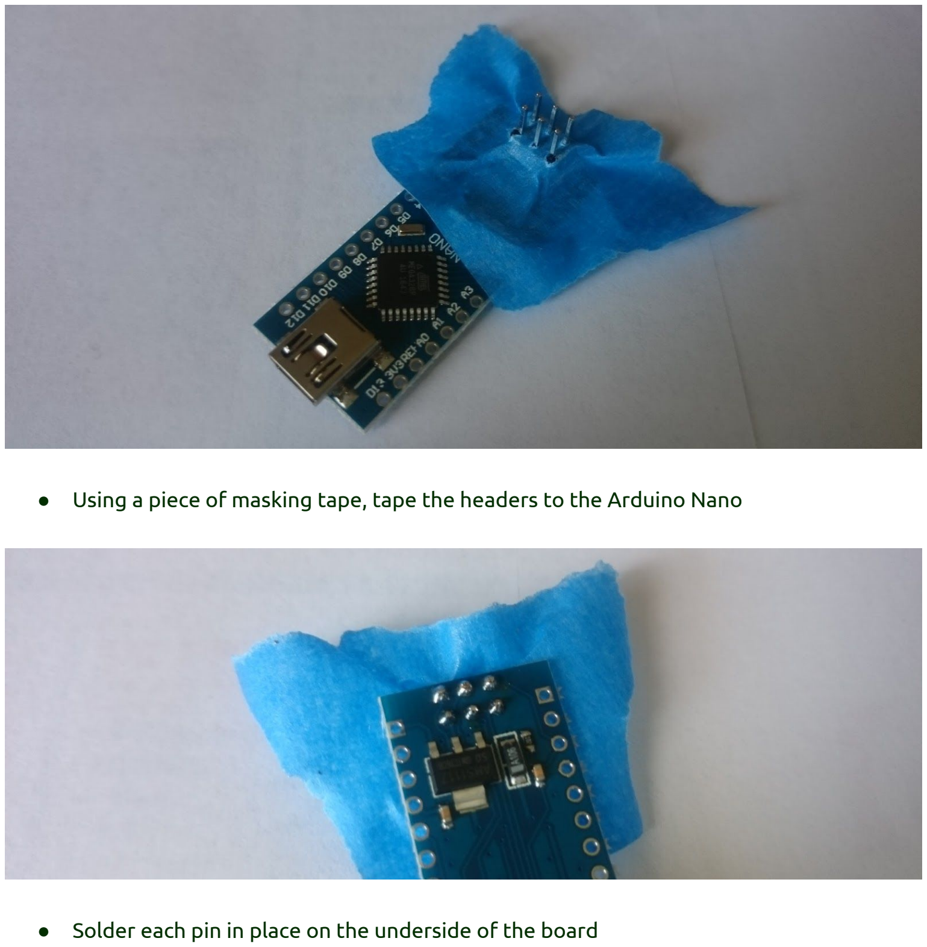
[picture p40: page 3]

- Using a piece of masking tape, tape the headers to the Arduino Nano
- Solder each pin in place on the underside of the board

# Step 2

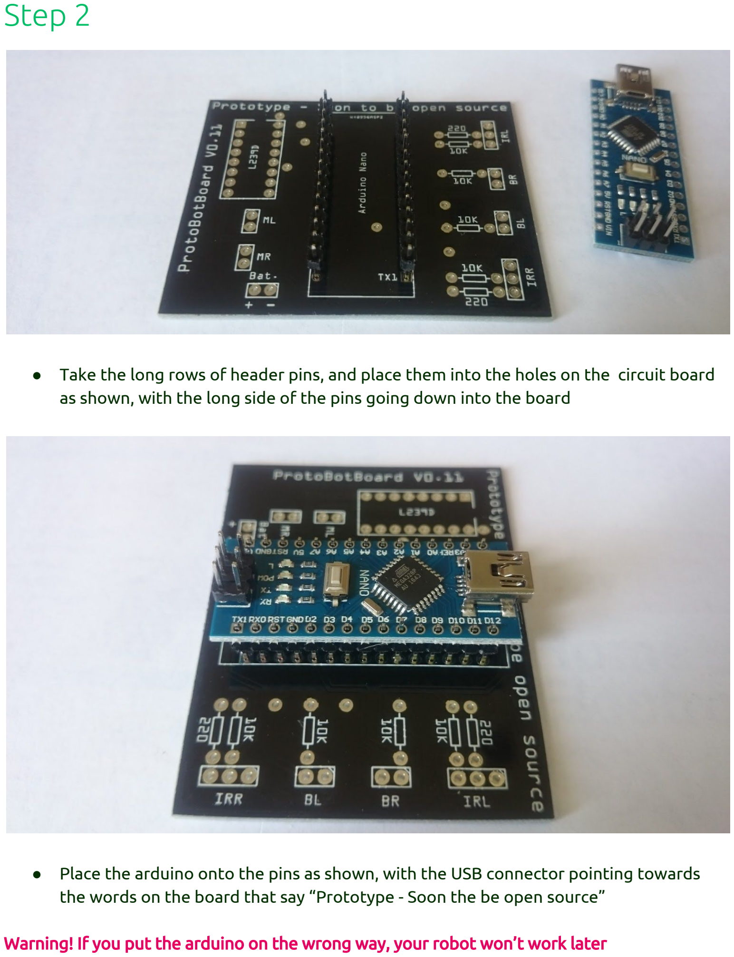
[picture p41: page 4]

- Take the long rows of header pins, and place them into the holes on the circuit board as shown, with the long side of the pins going down into the board
- Place the arduino onto the pins as shown, with the USB connector pointing towards the words on the board that say “Prototype - Soon the be open source”
Warning! | If | you | put | the | arduino | on | the | wrong | way, | your | robot | won’t | work | later

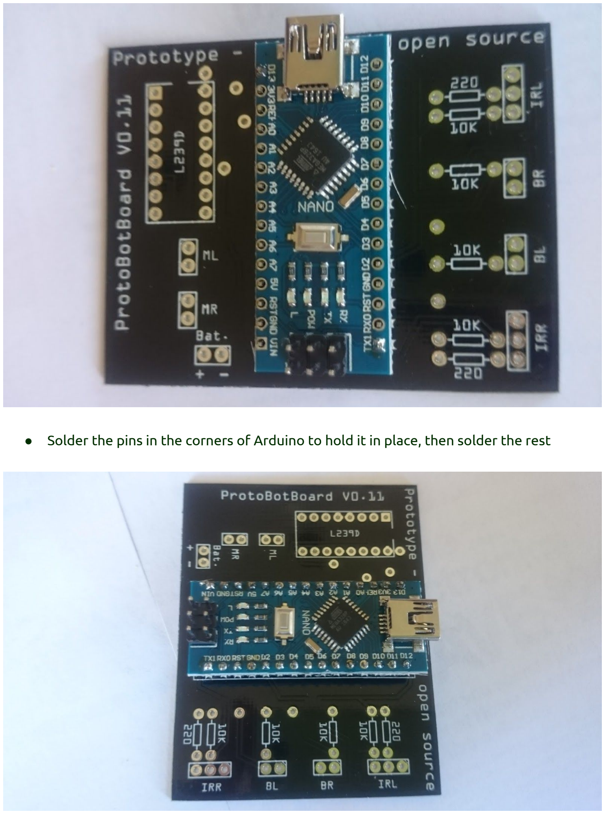
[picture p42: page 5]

- Solder the pins in the corners of Arduino to hold it in place, then solder the rest

# Step 3

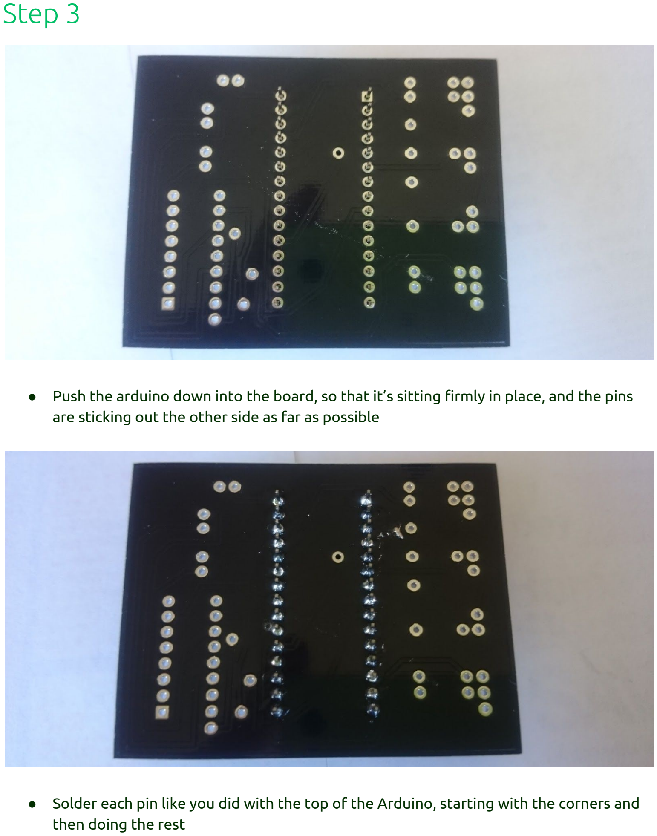
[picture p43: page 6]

- Push the arduino down into the board, so that it’s sitting firmly in place, and the pins are sticking out the other side as far as possible
- Solder each pin like you did with the top of the Arduino, starting with the corners and then doing the rest

# Step 4

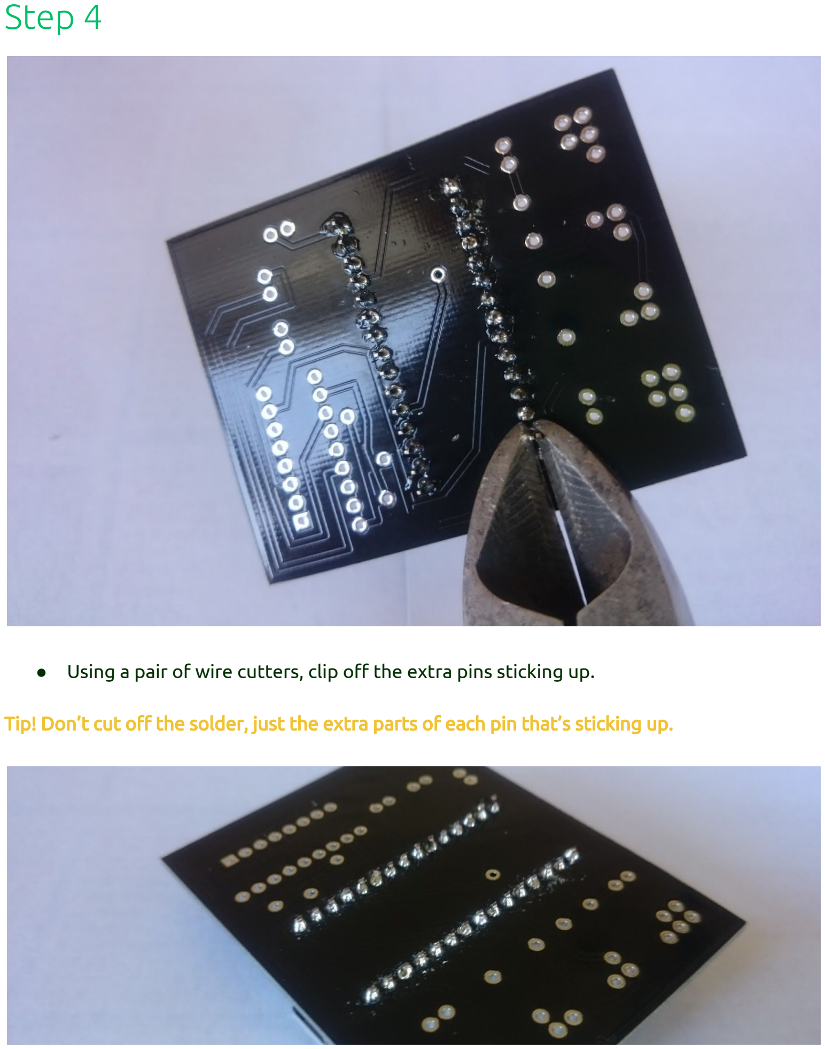
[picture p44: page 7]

- Using a pair of wire cutters, clip off the extra pins sticking up.
Tip! | Don’t | cut | off | the | solder, | just | the | extra | parts | of | each | pin | that’s | sticking | up.

# Step 5

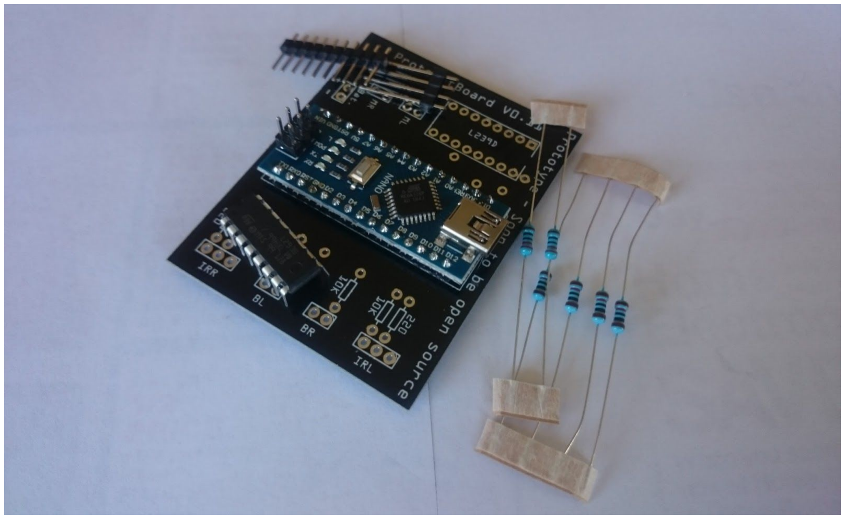
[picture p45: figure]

- Make sure you have all the other parts for the board

### You need:

- 2 x 220 Ohm resistors
- 4 x 10K Ohm resistors
- 1 x L293D (Motor Driver Chip)
- 4 x Long header pins
- 10 x short header pins
- 1 x female header pins

# Step 6


- Place the motor driver chip on the board, as shown. Make sure the notch in the top of the board is aligned as shown
Warning! | Be | careful | not | to | bend | or | break | the | pins | of | the | motor | driver!
- Solder the chip in, starting with the corners of the chip, then soldering the rest

# Step 7


- Find the two 220 Ohm resistors. They should look like one of the two kinds above
- Bend the leads at a 90 degree angle, and put them in the spots marked “220” on the board


- With the leads in the board, bend them at a slight angle to keep the resistors from falling out
Tip! | Put | a | piece | of | masking | tape | over | the | resistors | to | help | them | stay | in.
- Solder the leads, then clip the extra wire off with the wire cutters

# Step 8


- Find the four 10K Ohm resistors. They should look like one of the two kinds above
- As with the 220 Ohm resistors, bend the leads and insert them into the spots marked “10K”


- Bend the leads slightly to keep them from falling out
Tip! | You | can | use | masking | tape | here | too, | to | help | keep | the | resistors | in | place.
- Solder the leads, then clip off the extra wire

# Step 9


- Find the piece of long pin headers
- Break it in half by twisting each half in a different direction
Warning! | Make | sure | you | get | 2 | pins | on | each | half.


- Grab one end of the header with a pair of pliers, and bend it 90 degrees
- Repeat with the other header pin


- Insert the headers into the holes labelled “MR” and “ML”, as shown
- Put a piece of masking tape over the headers, to keep them in place
- Solder them in place, then remove the masking tape

# Step 10


- Break the short header pins into 4 pieces as shown - two 2 pin pieces, and two 3 pin pieces
- Use a few pieces of masking tape to hold the header pins in place.
Tip! | Your | board | will | look | nicer | if | the | pins | are | straight | up/down/side | to | side.


- Solder the header pins, and remove the masking tape
- Take the female header pins, and put it into the place marked “Bat.”
- Use a bit of masking tape to hold it in place


- Solder the pins in place, remove the masking tape, and clip off the extra wire

Congrats! Your board is finished.

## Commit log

2017-06-10 Add files via upload
    Assembly Guide for Current Protobot Version
2017-06-10 Add files via upload
    A newer version of the Base, plus some supports for the PCB instead of just hot-gluing it to the base.
    [ProtoBotPCBSupport.stl, ProtoBotV022.stl]
2017-06-10 Delete ProtoBotBase.stl
    Because it's outdated. Might re-add later with a different "old" name in case people want something to modify.
    [ProtoBotBase.stl]
2017-06-10 Delete ProtoBotSlider.stl
    Because it's outdated. Will probably reupload later with an "old" filename
    [ProtoBotSlider.stl]
2017-06-10 Add files via upload
    Reorganizing the repository
    [ProtoBotAntennae.stl, ProtoBotPCBSupport.stl, ProtoBotV022.stl]
2017-06-20 Add files via upload
    A guide for assembling the PCB.
2017-10-27 Adding the updated base and antenna designs
    [4Antenna.stl, Antenna.stl, Base.stl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]
2017-11-11 Adding Assembly guides
2017-11-16 Added newest board Gerber
2018-02-12 Added Motor soldering Guide
2018-02-15 Added guide for soldering IR Sensors
2018-02-23 Added fritzing file for PCB
    [ProtoBot031.fzz]
